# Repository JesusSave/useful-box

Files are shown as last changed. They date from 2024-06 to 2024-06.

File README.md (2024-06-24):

# V2 Upgrades:
Tested with [Arduino-cli](https://github.com/arduino/arduino-cli) 0.35.3 and 1.0.1.

## Programs changes:

(20240611): 
- fix bug: switch state detection
- random reaction case after 10 turns

## CAD: 
Origianl CAD in .step and .stl, new versions are mainly by Solidworks, FreeCAD, and OpenSCAD. 

Color printer uses Prusa XL.

## To do list...

lid:
- hide pins
- color text : 

fixed-lid: 
- snap fit for sensor
- pin hole for switch
- snap fit for servo
- text: open - close

box:
- left top hole support hinders servo body
- 4x top holes too big for 2.85mm pins
- lid joint too loose
- bottom servo base
- snap fit for chip 
- chip USB-C opening

## Purchashing parts (Poland local)
- 1X 18.02 PLN
[WEMOS D1 mini ESP8266 USB C](https://erli.pl/produkt/modul-wifi-wemos-d1-mini-esp8266-12f-arduino-iot,145459971)

- 1X 19.4 PLN
[APDS-9960 RGB, gesture and proximity sensor](https://erli.pl/produkt/czujnik-swiatla-rgb-i-wykrywacz-gestow-apds-9960,185037548)

- 2X 12.58 PLN
[Serwo SG-90 - micro - 180](https://erli.pl/produkt/serwo-modelarskie-9g-sg90-micro-180,187494326)

- 1X 4.73 PLN
[Przełącznik dźwigniowy pojedynczy (SPDT 3P)](https://erli.pl/produkt/przelacznik-dzwigniowy-pojedynczy-spdt-3p,170778687)

## PCB v2
pcb v2 scheme
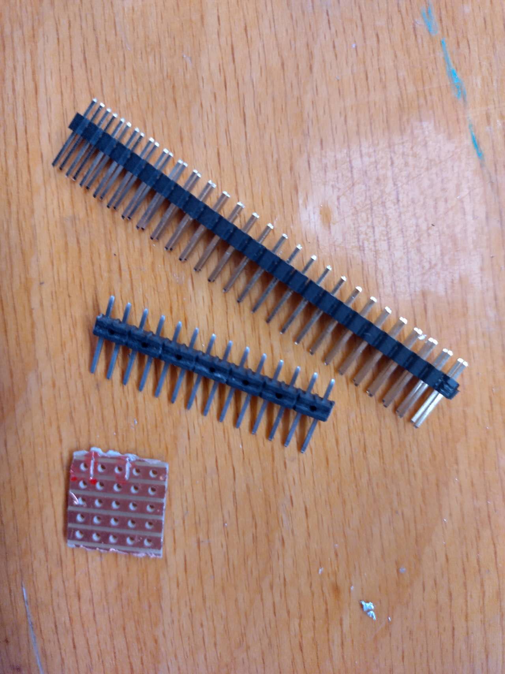
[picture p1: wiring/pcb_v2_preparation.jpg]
pcb v2 raw material preparation

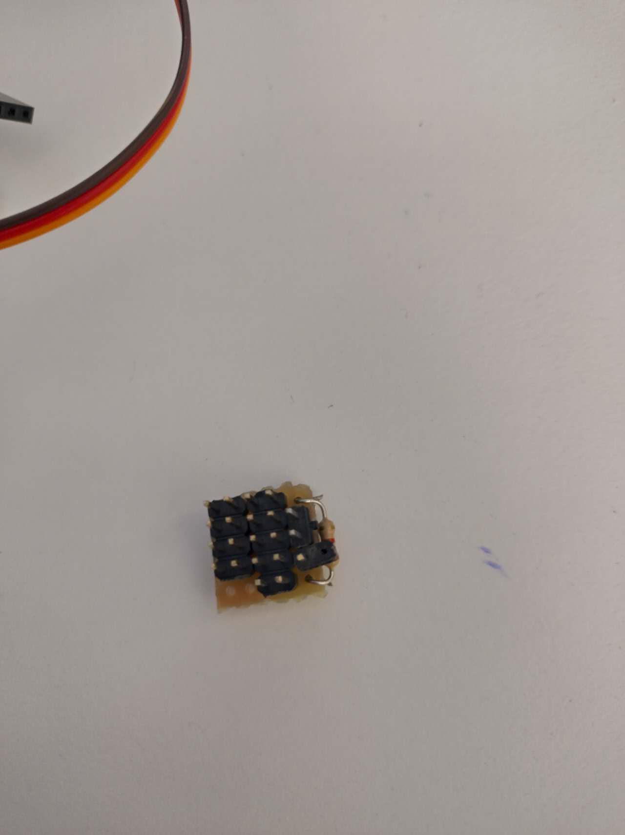
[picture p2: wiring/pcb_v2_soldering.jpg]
pcb v2 after soldering

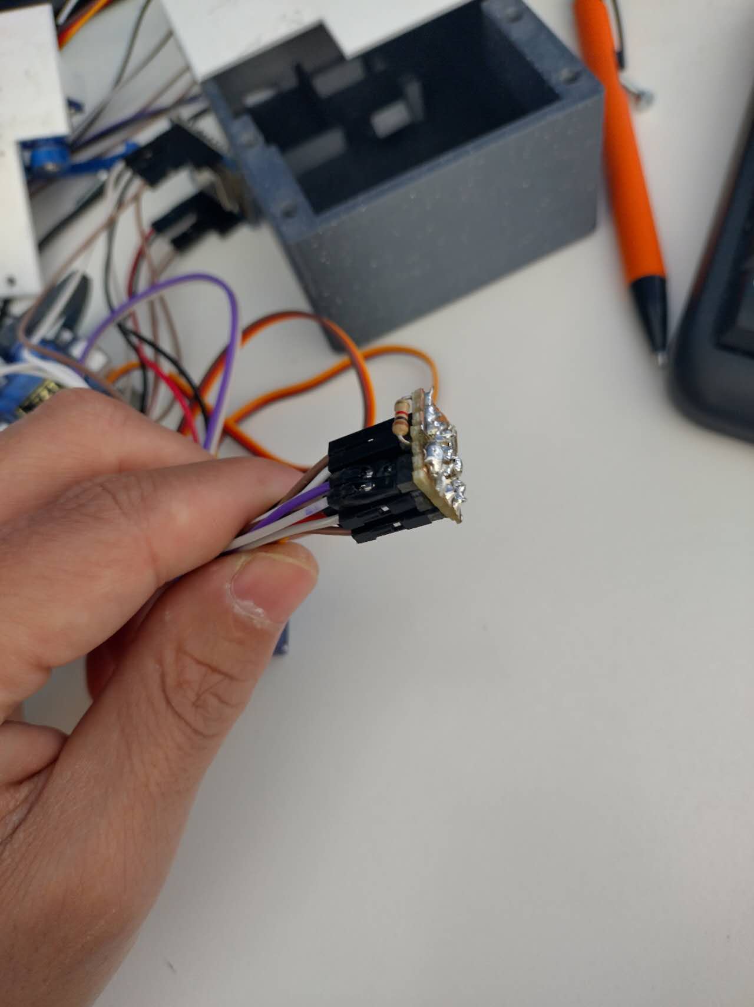
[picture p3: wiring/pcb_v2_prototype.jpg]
pcb v2 prototype

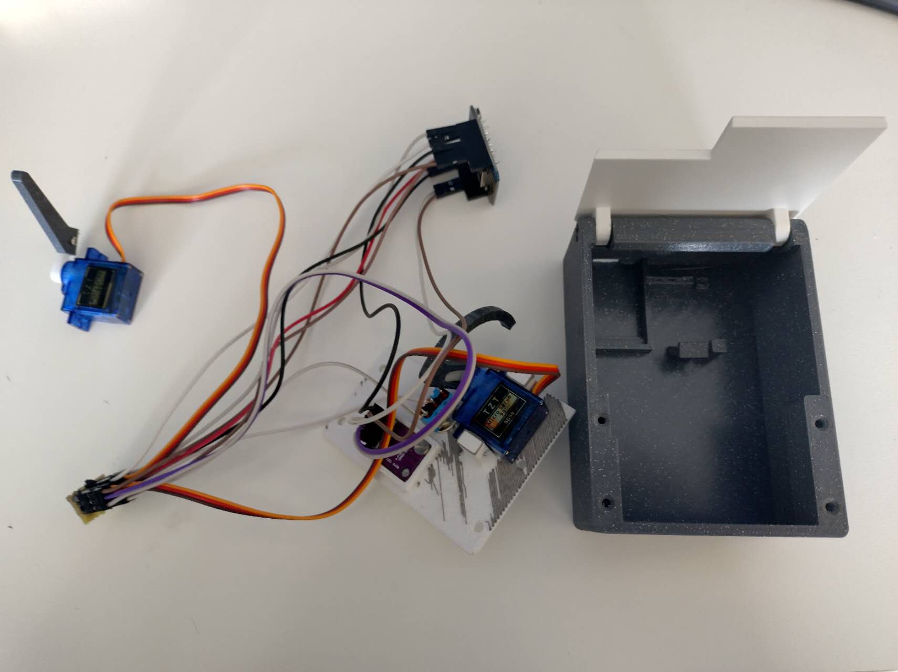
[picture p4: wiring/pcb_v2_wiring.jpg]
pcb v2 wiring


# ORIGINAL DOCUMENTATION OF [György Balássy](https://linkedin.com/in/balassy)
# Smart Useless Box with ESP8266 and Gesture Sensor

A useless box made smarter with an ESP8266 microcontroller on a Wemos D1 Mini board and an APDS-9960 proximity sensor to give more funny responses.



## YAUB (Yet Another Useless Box)?

Useless machines are not new, there are many versions available. You can create a simple one using a lever switch, however that will react always the same way. Using a programmable microcontroller you can create **funny, unexpected responses**, and by adding a proximity sensor you can surprise the user with **actions before she would even turn on the switch**!

This is a programmable useless box, so you have the option to implement **additional reactions** when you want to to further improve this funny little toy. What's more the used controller board has WiFi connectivity, so you can **connect it to other online services** (e.g. IFTTT) or **smart assistants** (Alexa, Cortana etc.).

## Smart Useless Box in Action

Click the image below to see this box in action:

Smart Useless Box in Action (http://www.youtube.com/watch?v=x0kGetj1nt8 "Smart Useless Box in Action")

## Hardware

The following hardware components are required to build this project:

- 1 × [Wemos D1 Mini board](https://wiki.wemos.cc/products:d1:d1_mini)
- 1 × [APDS-9960 RGB, gesture and proximity sensor](https://www.sparkfun.com/products/12787) - there are multiple versions of this board, use one that follows the pinout of the SparkFun module to simplify wiring. I used [this](https://www.aliexpress.com/item/32768898229.html) cheap one from AliExpress.
- 2 × [SG90 servo motors](https://components101.com/servo-motor-basics-pinout-datasheet)
- 1 × Switch - you have to test this to ensure it flips easily and the servo is strong enough to flip it, so I bought mine in the nearest electronics hardware store.
- 1 × 1kΩ resistance
- Male pin headers:
  - 1 × 1x2 for the switch
  - 2 × 1x3 for the servo motors
  - 1 × 1x5 for the sensor
- Prototype board or PCB - to create a shield for the Wemos D1 Mini.
- Pin headers - to connect the shield to the Wemos D1 Mini.
- Dupont cables or wires with connectors.
- BluTack - to mount the wires and the controller board.
- M3 screws - to mount the lids.

## Wiring

The wiring is designed to create a custom shield for the Wemos D1 Mini ESP8266 microcontroller-based board, instead of soldering the cables directly to the board. In this way you can easily assemble the parts or even reuse them in the future.

### Schematics

Schematic

### PCB

PCB

The PCB was designed with [Fritzing](https://fritzing.org), and you can [download the source file](./wiring/Useless-Box-Shield-v1.fzz) to further customize it to your needs.

You can also [download the Gerber files](./wiring/Useless-Box-Shield-v1-PCB-Gerber.zip) which you can use to order the PCB from your preferred PCB manufacturer. (Note: I've created my prototype manually then documented it in Fritzing, so I have not tested this PCB yet.)

## Software

The source code in this repo is created with [Visual Studio Code](https://code.visualstudio.com) using the [Arduino plugin from Microsoft](https://marketplace.visualstudio.com/items?itemName=vsciot-vscode.vscode-arduino), but it should work with the [Arduino IDE](https://www.arduino.cc/en/main/software) as well.

The code in this repository is preconfigured with the pin layout shown in the wiring diagram above, but if you decide to connect the parts to different pins, you have to update the values in the `config.h` file.

After finalizing the pin configuration (or using the default one) just upload the code to the Wemos D1 Mini board.

The responses of the box are implemented in the `useless-box.ino` file, and the `run()` function is responsible for selecting and executing the reaction to a flip of the switch or to a signal from the sensor. Feel free to add new logic or remove any existing reaction you don't like in this function.

## The Box

I designed a custom box for this project which can be 3D printed or even further customized. You can download the model from [Thingiverse](https://www.thingiverse.com/thing:3856965) or [MyMiniFactory](https://www.myminifactory.com/object/3d-print-100944).

Happy Printing! :)

## About the author

This project is maintained by [György Balássy](https://linkedin.com/in/balassy).

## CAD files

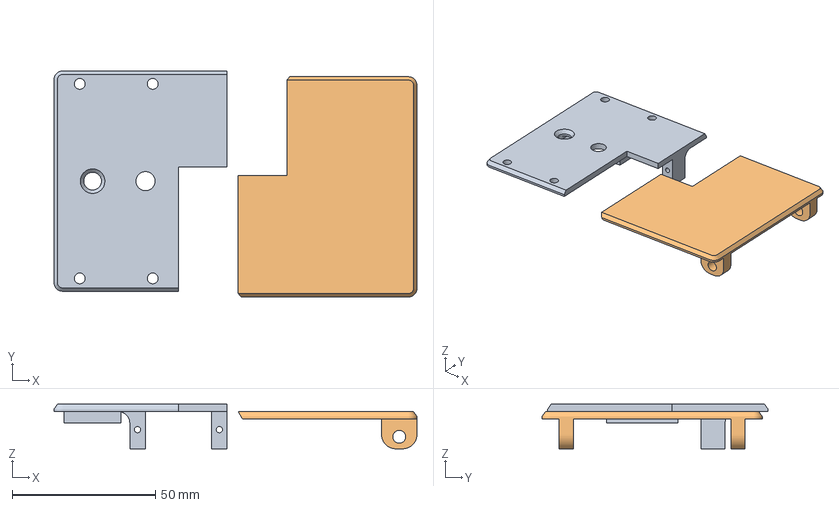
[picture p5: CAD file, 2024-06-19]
cad/smart-useless-box-2lids-v3.3mf
126.9 x 79.0 x 15.6 mm
smart-useless-box-fixed-lid-v3.stl
smart-useless-box-moving-lid-v1.stl

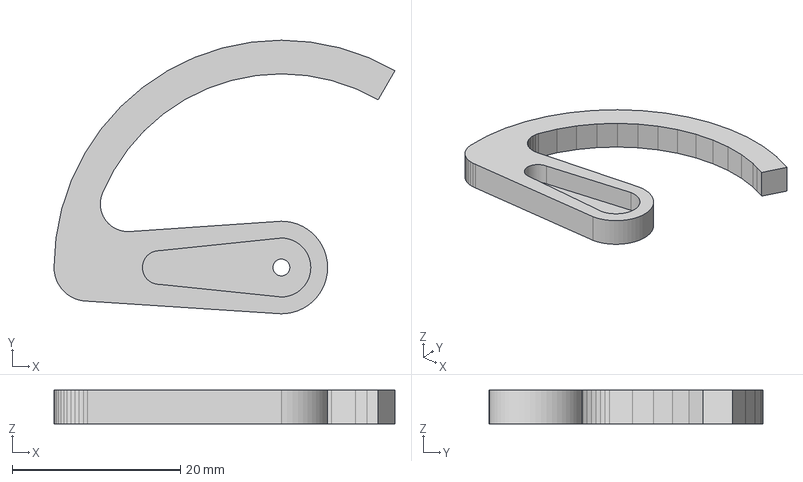
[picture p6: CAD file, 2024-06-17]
cad/smart-useless-box-switch-arm-v1.step
40.5 x 32.5 x 4.00 mm

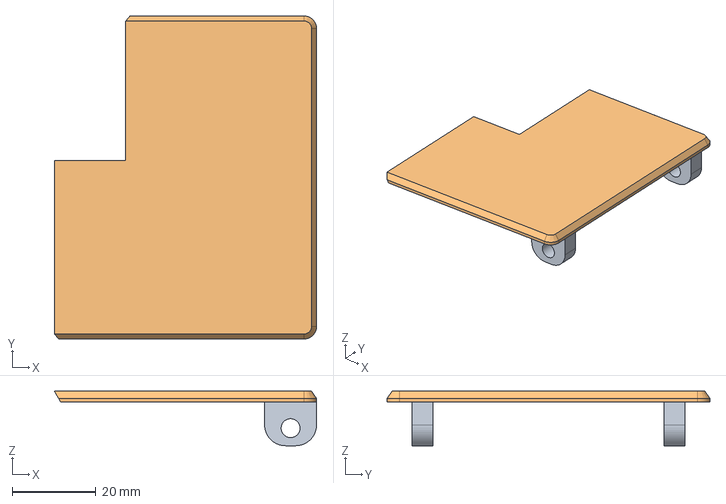
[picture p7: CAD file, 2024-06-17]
cad/smart-useless-box-moving-lid-v1.step
62.5 x 77.0 x 13.0 mm

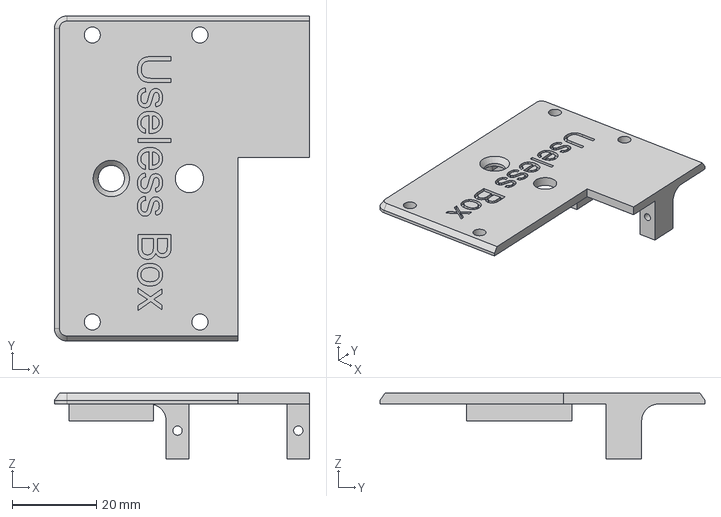
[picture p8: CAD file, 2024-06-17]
cad/smart-useless-box-fixed-lid-v1.step
60.5 x 77.0 x 15.6 mm

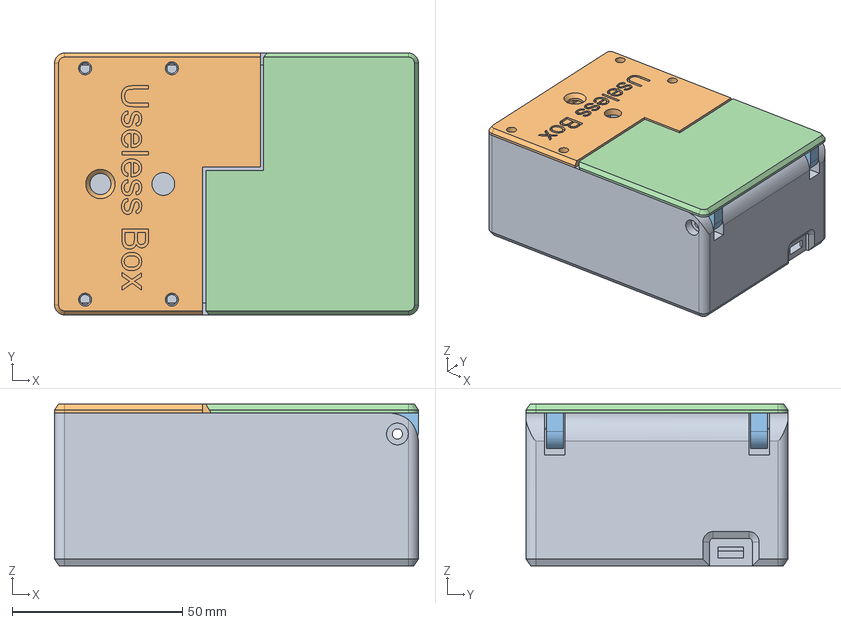
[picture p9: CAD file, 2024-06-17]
cad/smart-useless-box-box-v1.step
107.0 x 77.0 x 47.6 mm
Box Base
Fixed Lid
Moving Lid

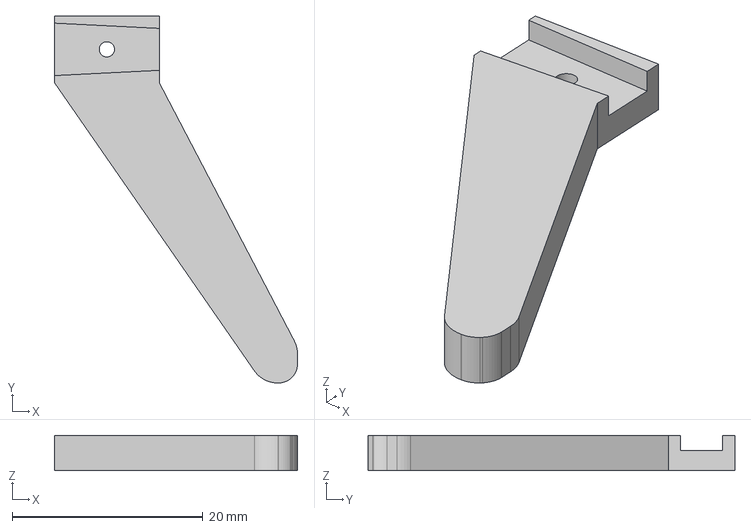
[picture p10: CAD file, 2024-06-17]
cad/smart-useless-box-lid-arm-v1.step
25.5 x 38.5 x 3.70 mm

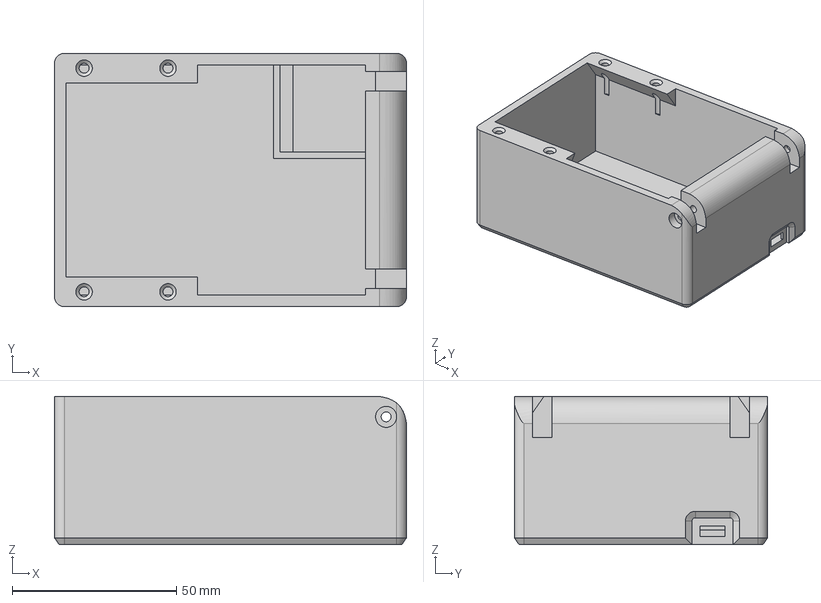
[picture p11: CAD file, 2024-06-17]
cad/smart-useless-box-base-v1.step
107.0 x 77.0 x 45.0 mm

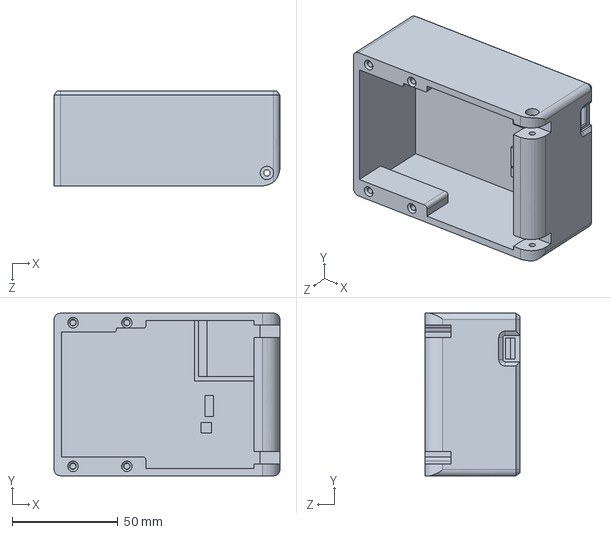
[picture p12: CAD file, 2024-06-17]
cad/smart-useless-box-base-v2.SLDPRT
107.0 x 77.0 x 45.0 mm

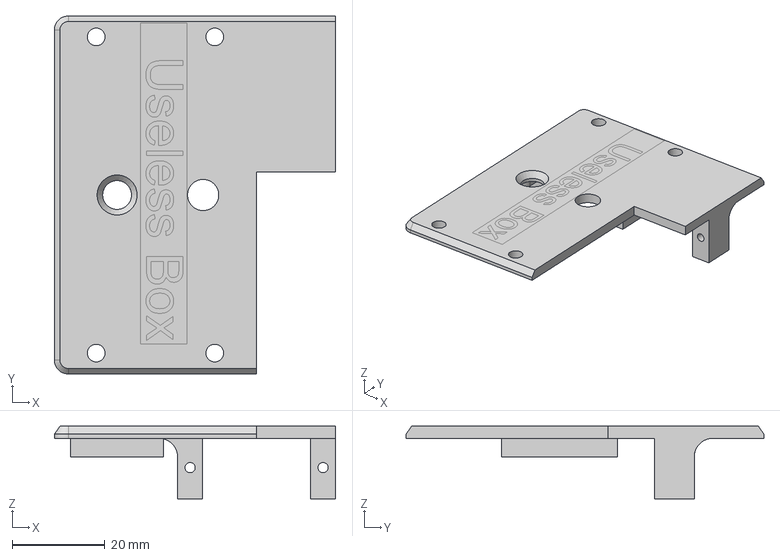
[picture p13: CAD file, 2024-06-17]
cad/smart-useless-box-fixed-lid-v3.FCStd
60.5 x 77.0 x 15.6 mm

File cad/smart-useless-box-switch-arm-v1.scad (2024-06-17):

import("/home/qchen/Documents/Techs/arduino/esp8266/useless-box/3d1/smart-useless-box-switch-arm-v1.stl", convexity=3);

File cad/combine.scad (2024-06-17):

module base1() {
    import("/home/qchen/Documents/Techs/arduino/esp8266/useless-box/3d1/smart-useless-box-base-v1.stl", convexity=3);
}

module base2() {
    import("/home/qchen/Documents/Techs/arduino/esp8266/useless-box/3d1/smart-useless-box-base-v2.STL", convexity=3); 
}

module esp8266() {
    import("/home/qchen/Documents/Editors/openscad/esp8266/ESP8266WemosD1mini.stl", convexity=3);
}

// Position and rotate the ESP8266 module
rotate([0, 0,90])  // Adjust the rotation angles as needed
translate([-8.2, -58, 6])  // Adjust the translation values as needed
color("red") 
esp8266();

/*
color("green") 
base1();
*/

translate([-53.5, -39.35, 0]) // Adjust values based on half of base2's dimensions
base2();

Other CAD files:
cad/smart-useless-box-fixed-lid-v2.SLDPRT
cad/smart-useless-box-base-v1.stl
cad/smart-useless-box-base-v2.STL
cad/smart-useless-box-fixed-lid-v1.stl
cad/smart-useless-box-fixed-lid-v2.STL
cad/smart-useless-box-fixed-lid-v3.3mf
cad/smart-useless-box-fixed-lid-v3.stl
cad/smart-useless-box-lid-arm-v1.stl
cad/smart-useless-box-moving-lid-v1.stl
cad/smart-useless-box-switch-arm-v1.stl

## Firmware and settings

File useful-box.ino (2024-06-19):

/*
20240605: this is origial from 
https://github.com/balassy/useless-box.git

$ cat /etc/os-release 
PRETTY_NAME="Ubuntu 24.04 LTS"
NAME="Ubuntu"
VERSION_ID="24.04"
VERSION="24.04 LTS (Noble Numbat)"
VERSION_CODENAME=noble
ID=ubuntu
ID_LIKE=debian
HOME_URL="https://www.ubuntu.com/"
SUPPORT_URL="https://help.ubuntu.com/"
BUG_REPORT_URL="https://bugs.launchpad.net/ubuntu/"
PRIVACY_POLICY_URL="https://www.ubuntu.com/legal/terms-and-policies/privacy-policy"
UBUNTU_CODENAME=noble
LOGO=ubuntu-logo

$ arduino-cli version
arduino-cli  Version: 0.35.3 Commit: 95cfd654 Date: 2024-02-19T13:24:24Z
arduino-cli  Version: 1.0.0 Commit: 05c9852a Date: 2024-06-12T14:13:32Z

Used library Version Path
Servo        1.0.2   /home/qchen/.arduino15/packages/esp8266/hardware/esp8266/3.1.2/libraries/Servo                                                                     
Wire         1.0     /home/qchen/.arduino15/packages/esp8266/hardware/esp8266/3.1.2/libraries/Wire                                                                      

Used platform   Version Path
esp8266:esp8266 3.1.2   /home/qchen/.arduino15/packages/esp8266/hardware/esp8266/3.1.2                                                                                  
*/
// Platform libraries.
#include <Arduino.h>  // To add IntelliSense for platform constants.

// Third-party libraries.

// My classes.
#include "speed-servo.h"
#include "status-led.h"
#include "proximity-sensor.h"

#include "config.h"  // To store configuration and secrets.

SpeedServo lidServo;
SpeedServo switchServo;
StatusLed led;
ProximitySensor sensor;

int lastSwitchState = 0;
long playCount = 0;
bool isLidOpen = false;
bool monitorSensor = false;

void setup() {
  initSerial();
  initServos();
  initLed();
  initSensor();
  pinMode(PIN_SWITCH, INPUT);

  Serial.printf("Application version: %s\n", APP_VERSION);
  Serial.println("Setup completed.");
}

void initSerial() {
  Serial.begin(115200);
  Serial.println();
  Serial.println("Initializing serial connection DONE.");
}

void initServos() {
  lidServo.attach(PIN_LID_SERVO);
  lidServo.moveNowTo(LID_START_POSITION);

  switchServo.attach(PIN_SWITCH_SERVO);
  switchServo.moveNowTo(SWITCH_START_POSITION);
}

void initLed() {
  led.setPin(LED_BUILTIN);
  led.turnOff();
}

void initSensor() {
  sensor.attach(PIN_SENSOR_SDA, PIN_SENSOR_SCL, SENSOR_TRIGGER_THRESHOLD);
}

void loop() {
  int switchState = digitalRead(PIN_SWITCH);
  boolean isSwitchTurnedOn = (switchState == LOW);

  if (isSwitchTurnedOn) {
    led.turnOn();
    run();
    isLidOpen = false;
    led.turnOff();
  }

  // Check the proximity sensor even if the switch is not turned on.
  if (sensor.isInRange()) {
    if (!isLidOpen && monitorSensor) {
      openLidFast();
      isLidOpen = true;
    }
  } else {
    if (isLidOpen) {
      closeLidFast();
      isLidOpen = false;
    }
  }

  // Update last switch state for the next iteration.
  lastSwitchState = switchState;

  // Wait 250 ms before next reading (required for the sensor).
  delay(250);
}
void run() {
  static int runCounter = 0; // Counter to track the number of runs

  if (runCounter < 10) { // Follow pattern for the first 10 runs
    switch (runCounter % 10) { // Use runCounter to determine the pattern
      case 0:
      case 1:
        runSlow();
        break;
      case 2:
        runWaitThenFast();
        break;
      case 3:
        runFast();
        break;
      case 4:
        runFastThenClap();
        monitorSensor = true;
        break;
      case 5:
        runOpenCloseThenFast();
        monitorSensor = false;
        break;
      case 6:
        runPeekThenFast();
        break;
      case 7:
        runFastWithDelay();
        monitorSensor = true;
        break;
      case 8:
        runClap();
        monitorSensor = false;
        break;
      case 9:
        runHalf();
        break;
      default:
        break;
    }
  } else { // After 10 runs, switch to random selection
    int randomCase = random(10); // Generate a random number between 0 and 9

    switch (randomCase) {
      case 0:
        runSlow();
        break;
      case 1:
        runWaitThenFast();
        break;
      case 2:
        runFast();
        break;
      case 3:
        runFastThenClap();
        monitorSensor = true;
        break;
      case 4:
        runOpenCloseThenFast();
        monitorSensor = false;
        break;
      case 5:
        runPeekThenFast();
        break;
      case 6:
        runFastWithDelay();
        monitorSensor = true;
        break;
      case 7:
        runClap();
        monitorSensor = false;
        break;
      case 8:
        runHalf();
        break;
      case 9:
        // Add additional cases here as needed
        break;
      default:
        break;
    }
  }

  runCounter++; // Increment the run counter
  playCount++;
}

void runSlow() {
  openLidSlow();
  flipSwitchSlow();
  closeLidSlow();
}

void runWaitThenFast() {
  delay(5000);
  flipSwitchFast();
}

void runFast() {
  flipSwitchFast();
}

void runFastThenClap() {
  flipSwitchFast();
  clapLid();
}

void runOpenCloseThenFast() {
  openLidSlow();
  delay(2000);
  closeLidSlow();
  delay(2000);
  flipSwitchFast();
}

void runPeekThenFast() {
  switchServo.moveSlowTo(SWITCH_HALF_POSITION);
  delay(3000);
  switchServo.moveFastTo(SWITCH_START_POSITION);
  delay(3000);
  flipSwitchFast();
}

void runFastWithDelay() {
  openLidSlow();
  delay(4000);
  flipSwitchFast();
  closeLidFast();
}

void runClap() {
  clapLid();
  clapLid();
  clapLid();
  clapLid();
  openLidFast();
  flipSwitchFast();
  closeLidFast();
}

void runHalf() {
  switchServo.moveSlowTo(SWITCH_HALF_POSITION);
  delay(3000);
  switchServo.moveFastTo(SWITCH_END_POSITION);
  switchServo.moveFastTo(SWITCH_START_POSITION);
}

void openLidSlow() {
  lidServo.moveSlowTo(LID_END_POSITION);
}

void openLidFast() {
  lidServo.moveFastTo(LID_END_POSITION);
}

void closeLidSlow() {
  lidServo.moveSlowTo(LID_START_POSITION);
}

void closeLidFast() {
  lidServo.moveFastTo(LID_START_POSITION);
}

void clapLid() {
  openLidFast();
  closeLidFast();
}

void flipSwitchSlow() {
  switchServo.moveSlowTo(SWITCH_END_POSITION);
  switchServo.moveSlowTo(SWITCH_START_POSITION);
}

void flipSwitchFast() {
  switchServo.moveFastTo(SWITCH_END_POSITION);
  switchServo.moveFastTo(SWITCH_START_POSITION);
}

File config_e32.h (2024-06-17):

const char* APP_VERSION = "0.0.1";

#ifndef LED_BUILTIN
#define LED_BUILTIN 4
#endif

const int PIN_LID_SERVO = 8;     // The GPIO number of the pin where the lid opener servo is connected.
const int PIN_SWITCH_SERVO = 0;  // The GPIO number of the pin where the switch manipulator servo is connected.
const int PIN_SWITCH = 5;        // The GPIO number of the pin where the switch is connected.
const int PIN_SENSOR_SDA = 2;    // The GPIO number of the pin where the SDA pin of the APDS-9660 sensor is connected.
const int PIN_SENSOR_SCL = 1;    // The GPIO number of the pin where the SCL pin of the APDS-9660 sensor is connected.
const uint8_t SENSOR_TRIGGER_THRESHOLD = 100;  // The proximity value level that triggers a lid opening. (lower=brighter, higher=darker)

const int LID_START_POSITION = 90;
const int LID_END_POSITION = 40;
const int SWITCH_START_POSITION = 0;
const int SWITCH_END_POSITION = 145;
const int SWITCH_HALF_POSITION = 90;

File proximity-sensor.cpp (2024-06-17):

#include "proximity-sensor.h"

void ProximitySensor::attach(uint8_t sdaPin, uint8_t sclPin, uint8_t rangeThreshold) {
  Serial.println(F("ProximitySensor: Initializing..."));

  _sensor = SparkFun_APDS9960();

  Serial.println(F("ProximitySensor: Starting I2C..."));
  Wire.begin(sdaPin, sclPin);
  Serial.println(F("ProximitySensor: Starting I2C...DONE"));

  Serial.println(F("ProximitySensor: Configuring I2C and initial values..."));
  if (_sensor.init()) {
    Serial.println(F("ProximitySensor: Configuring I2C and initial values...DONE"));
  } else {
    Serial.println(F("ProximitySensor: Configuring I2C and initial values...FAILED!"));
  }

  Serial.println(F("ProximitySensor: Adjusting the sensor gain..."));
  if (_sensor.setProximityGain(PGAIN_2X)) {
    Serial.println(F("ProximitySensor: Adjusting the sensor gain...DONE"));
  } else {
    Serial.println(F("ProximitySensor: Adjusting the sensor gain...FAILED!"));
  }

  Serial.println(F("ProximitySensor: Starting the sensor..."));
  bool enableInterrupts = false;
  if (_sensor.enableProximitySensor(enableInterrupts)) {
    Serial.println(F("ProximitySensor: Starting the sensor...DONE"));
  } else {
    Serial.println(F("ProximitySensor: Starting the sensor...FAILED!"));
  }

  _rangeThreshold = rangeThreshold;

  Serial.println(F("ProximitySensor: Initializing...DONE"));
}

uint8_t ProximitySensor::getProximity() {
  if ( _sensor.readProximity(_lastProximityValue) ) {
    Serial.print(F("ProximitySensor: Proximity value: "));
    Serial.println(_lastProximityValue);
    return _lastProximityValue;
  } else {
    Serial.println(F("ProximitySensor: Reading proximity value FAILED!"));
    // 确保在所有情况下都有一个返回值
    return 0; // 或者返回一个适当的默认值
  }
}

bool ProximitySensor::isInRange() {
  uint8_t currentProximityValue = getProximity();
  return currentProximityValue > _rangeThreshold;
}

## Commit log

2024-06-17 Add new files with modifications
    [combine.scad, smart-useless-box-base-v1.step, smart-useless-box-base-v1.stl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]
2024-06-19 pcb v2
    [smart-useless-box-2lids-v3.3mf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]
2024-06-24 tested with Arduino-cli 1.0.1
